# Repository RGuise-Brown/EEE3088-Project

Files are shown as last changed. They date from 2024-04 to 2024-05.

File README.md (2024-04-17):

# EEE3088-Project
This repository is used for the collaborative project to create a micromouse with the focus on creating a power and sensing unit which will work with an existing structure, motherboard and processor.This project is being completed by Rachael Guise-Brown and Heinrich Crous for EEE3088F at UCT.

Project Overview:

The project involves building subassemblies for a micro-mouse robot designed to navigate a maze within a set time limit. This repository focuses on the design and fabrication of the following modules:

Power Module: This module will be responsible for powering the motors, charging the battery, switching the robot on and off and providing an indication of the battery level to the processor.
Sensor Module: This module  will be responsible for detecting objects in the maze environment and relaying this information to the processor for navigation purposes.

Folder Structure:
power_module: This folder will contain all schematics, PCB design files, component selection information, and testing procedures related to the power module.
sensor_module: This folder will contain all design files, documentation, and testing procedures related to the sensor module.
documentation: This folder will contain any information documents linked to both power and sensor modules.

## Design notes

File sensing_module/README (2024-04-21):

This folder contains the following files:
1. My circuit schematic
2. Screenshots of the front and back of my PCB
3. A screenshot of my PCB in 3D viewer
4. My gerber files
5. My production files
6. My JLCPCB acceptance files
7. Datasheets for the TSAL4400, PD333, AND 2N3904

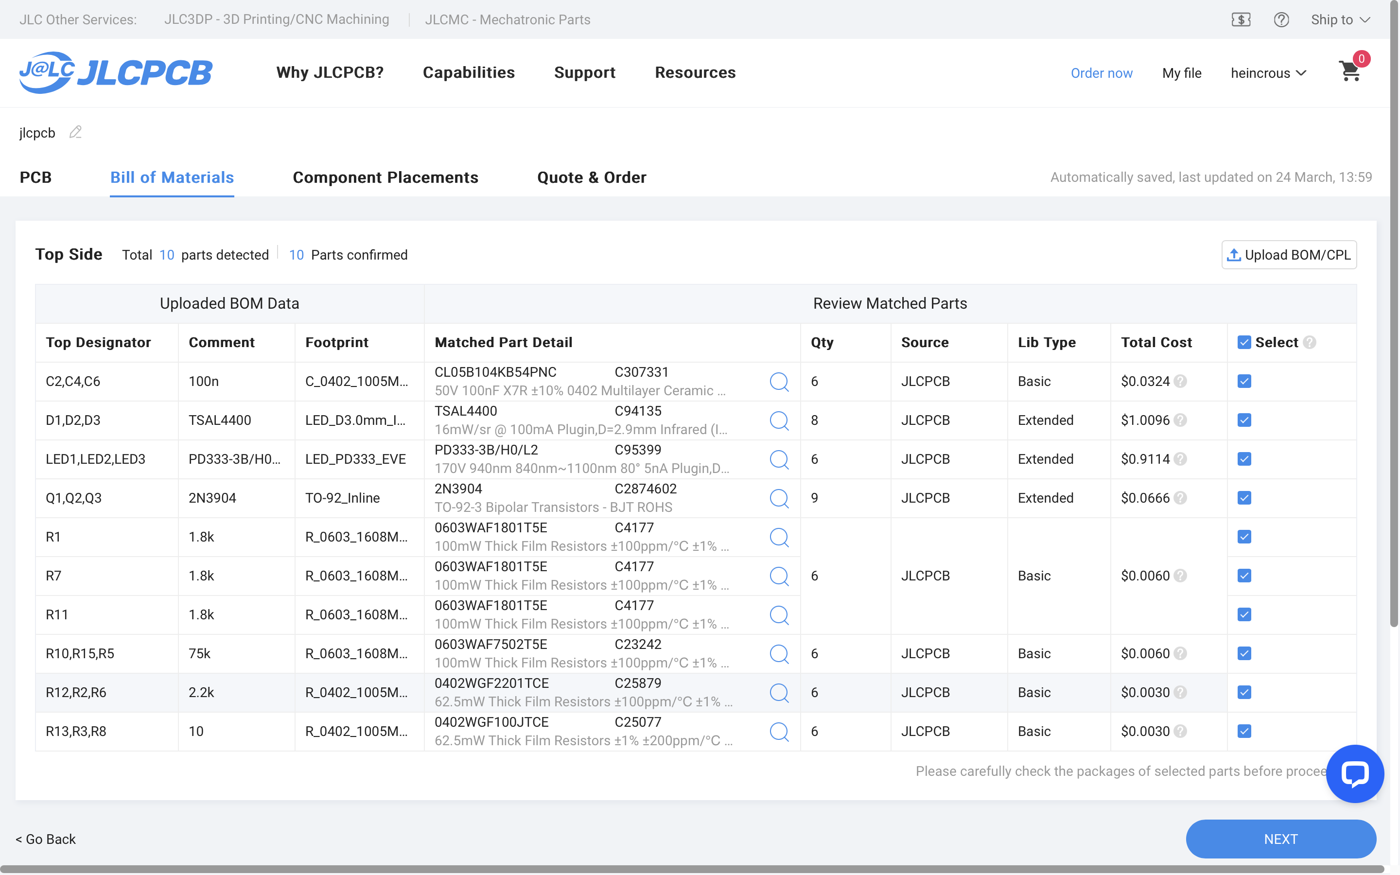
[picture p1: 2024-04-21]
sensing_module/production/EEE3088F_Project_JLCPCBBOM_CRSHEI004.png

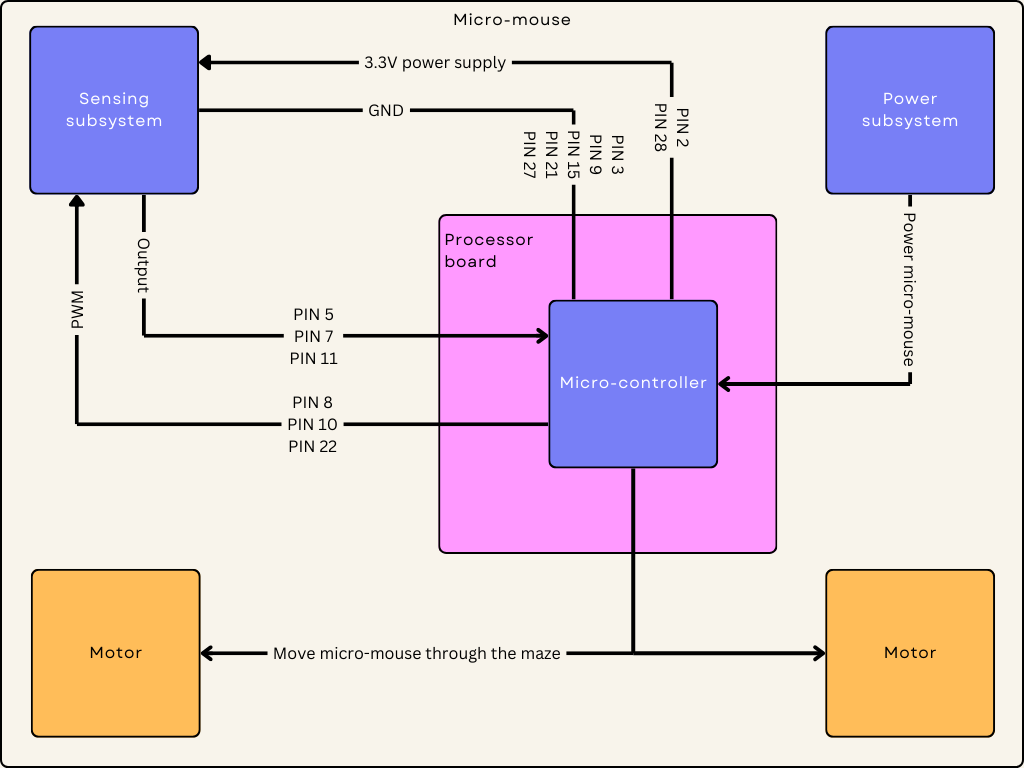
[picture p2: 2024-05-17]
sensing_module/Integration.png

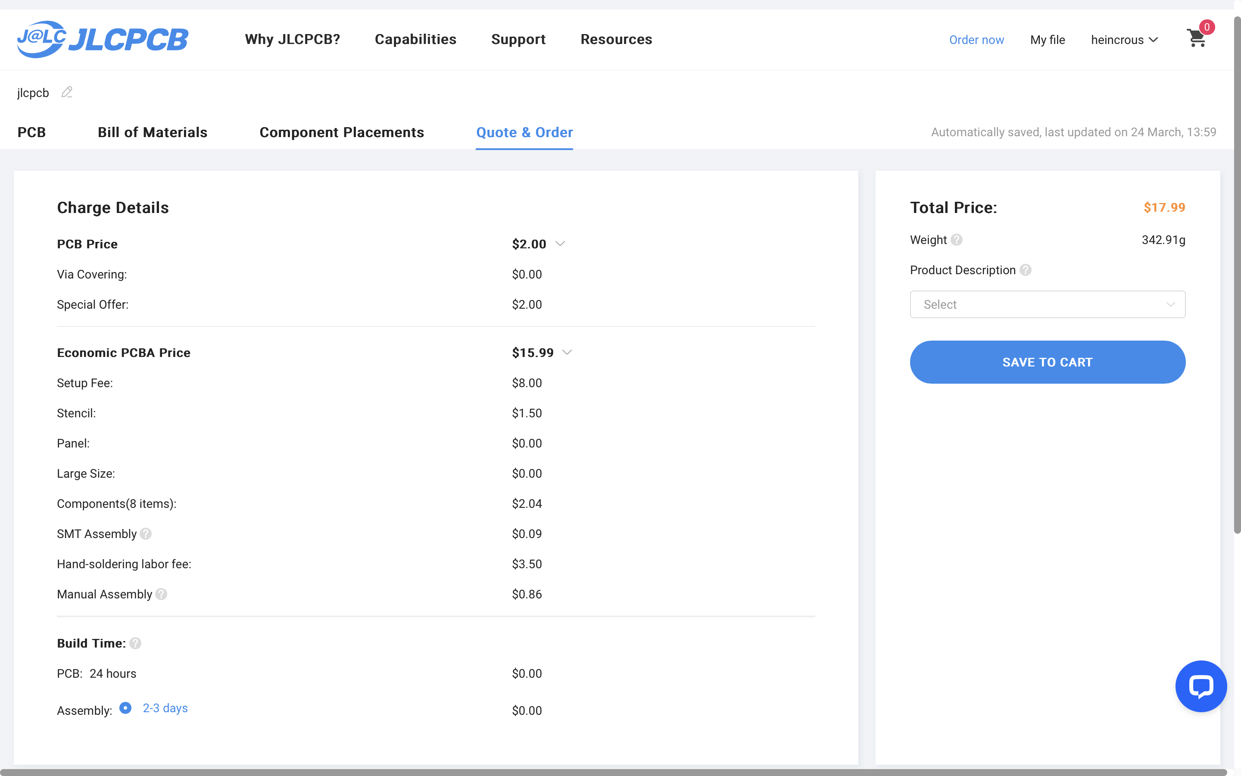
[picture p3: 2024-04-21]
sensing_module/acceptance/EEE3088F_Project_JLCPCBacceptance1_CRSHEI004.png

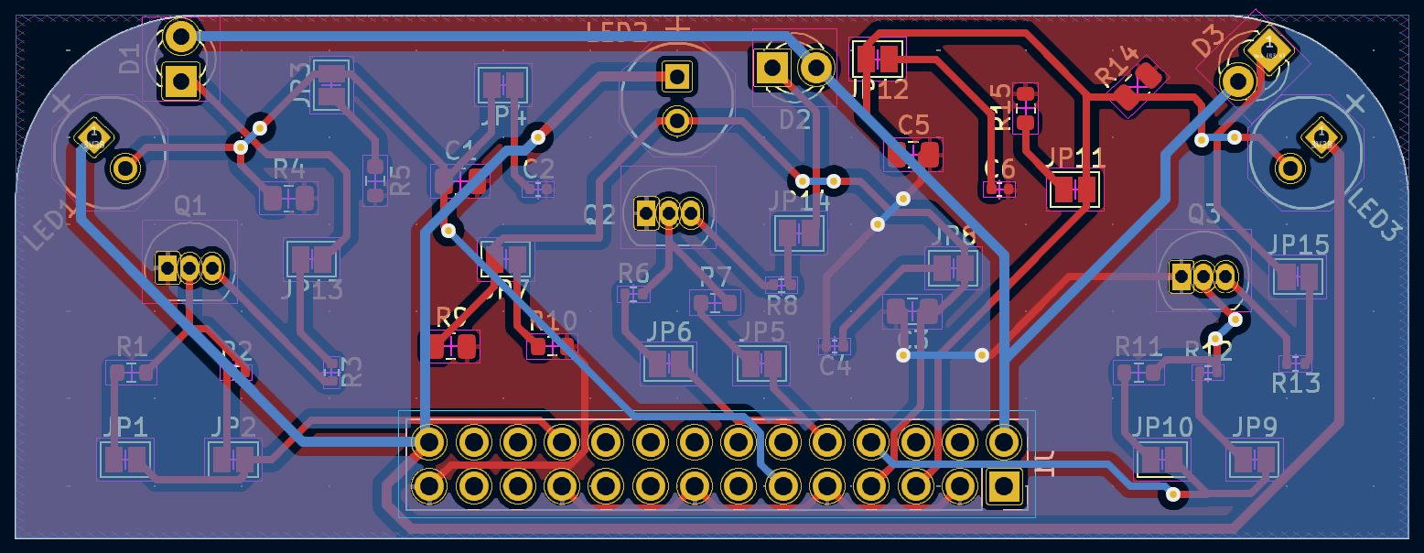
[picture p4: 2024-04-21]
sensing_module/Back.png

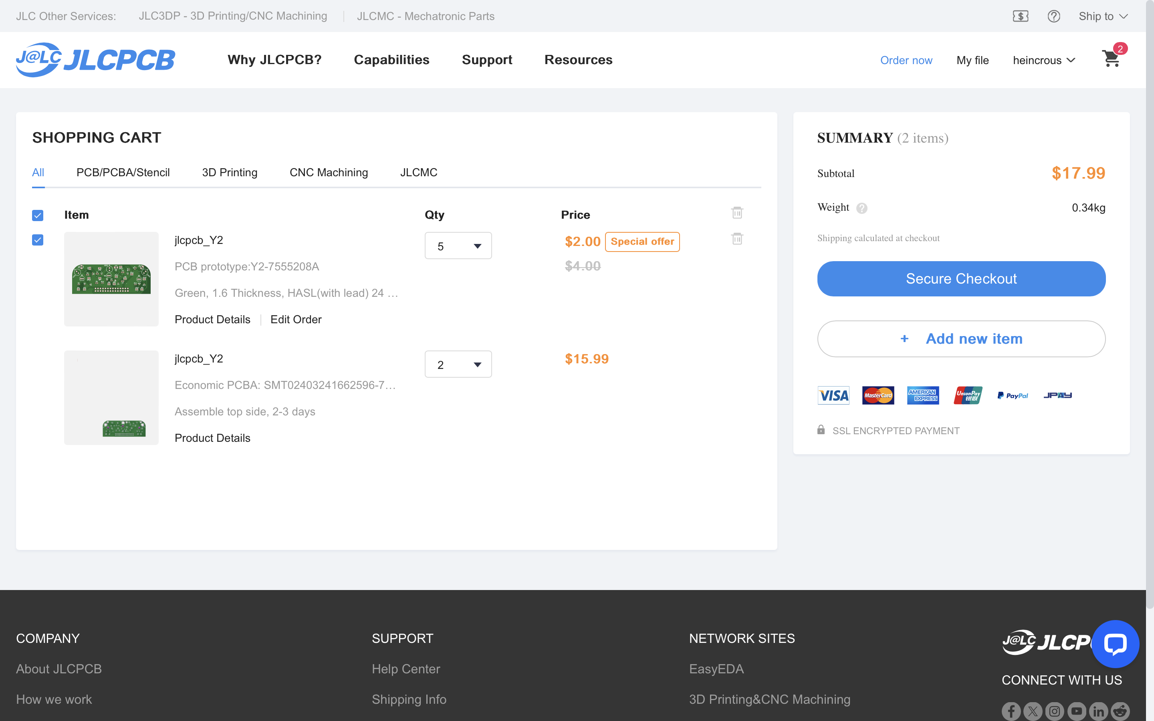
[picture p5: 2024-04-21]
sensing_module/acceptance/EEE3088F_Project_JLCPCBacceptance2_CRSHEI004.png

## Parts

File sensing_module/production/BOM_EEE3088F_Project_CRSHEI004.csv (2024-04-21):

Comment | Designator | Footprint | LCSC
75k | R10,R15,R5 | R_0603_1608Metric | C23242
10 | R13,R3,R8 | R_0402_1005Metric | C25077
2.2k | R12,R2,R6 | R_0402_1005Metric | C25879
2N3904 | Q1,Q2,Q3 | TO-92_Inline | C2874602
100n | C2,C4,C6 | C_0402_1005Metric | C307331
TSAL4400 | D1,D2,D3 | LED_D3.0mm_IRBlack | C94135
PD333-3B/H0/L2 | LED1,LED2,LED3 | LED_PD333_EVE | C95399
1.8k | R1 | R_0603_1608Metric
1.8k | R7 | R_0603_1608Metric
1.8k | R11 | R_0603_1608Metric

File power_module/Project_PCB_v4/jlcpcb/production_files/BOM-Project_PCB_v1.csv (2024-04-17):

Comment | Designator | Footprint | LCSC
1.2kR | R1 | R_0805_2012Metric | C17379
100R | R100,R_Fault1 | R_0805_2012Metric | C17408
10k | R10k1 | R_0805_2012Metric | C17414
1k | R1k1 | R_0805_2012Metric | C17513
3.0kR | R2,R3k1 | R_0805_2012Metric | C17661
470R | R_Stat1 | R_0805_2012Metric | C17710
510 | R510 | R_0805_2012Metric | C17734
2k | R_Prog1 | R_1206_3216Metric | C17944
4.7uF | C_Batt1,C_Vdd1 | C_0603_1608Metric | C19666
10uF | C_Vm1 | C_0603_1608Metric | C19702
LED_Red | D_Stat1 | LED_0603_1608Metric | C2286
LED_Green | Fault1 | LED_0805_2012Metric | C2297
2.2uF | C_Vint1 | C_0603_1608Metric | C23630
5.1k | R5.1 | R_0805_2012Metric | C27834
SS-12D10L5 | S1 | SW-TH_SS-12D10L5 | C319012
MCP73831-2-OT | Charge1 | SOT-23-5 | C424093
DRV8833PW | MD1 | TSSOP-16_4.4x5mm_P0.65mm | C50506
10nF | C_Vcp1 | C_0603_1608Metric | C57112

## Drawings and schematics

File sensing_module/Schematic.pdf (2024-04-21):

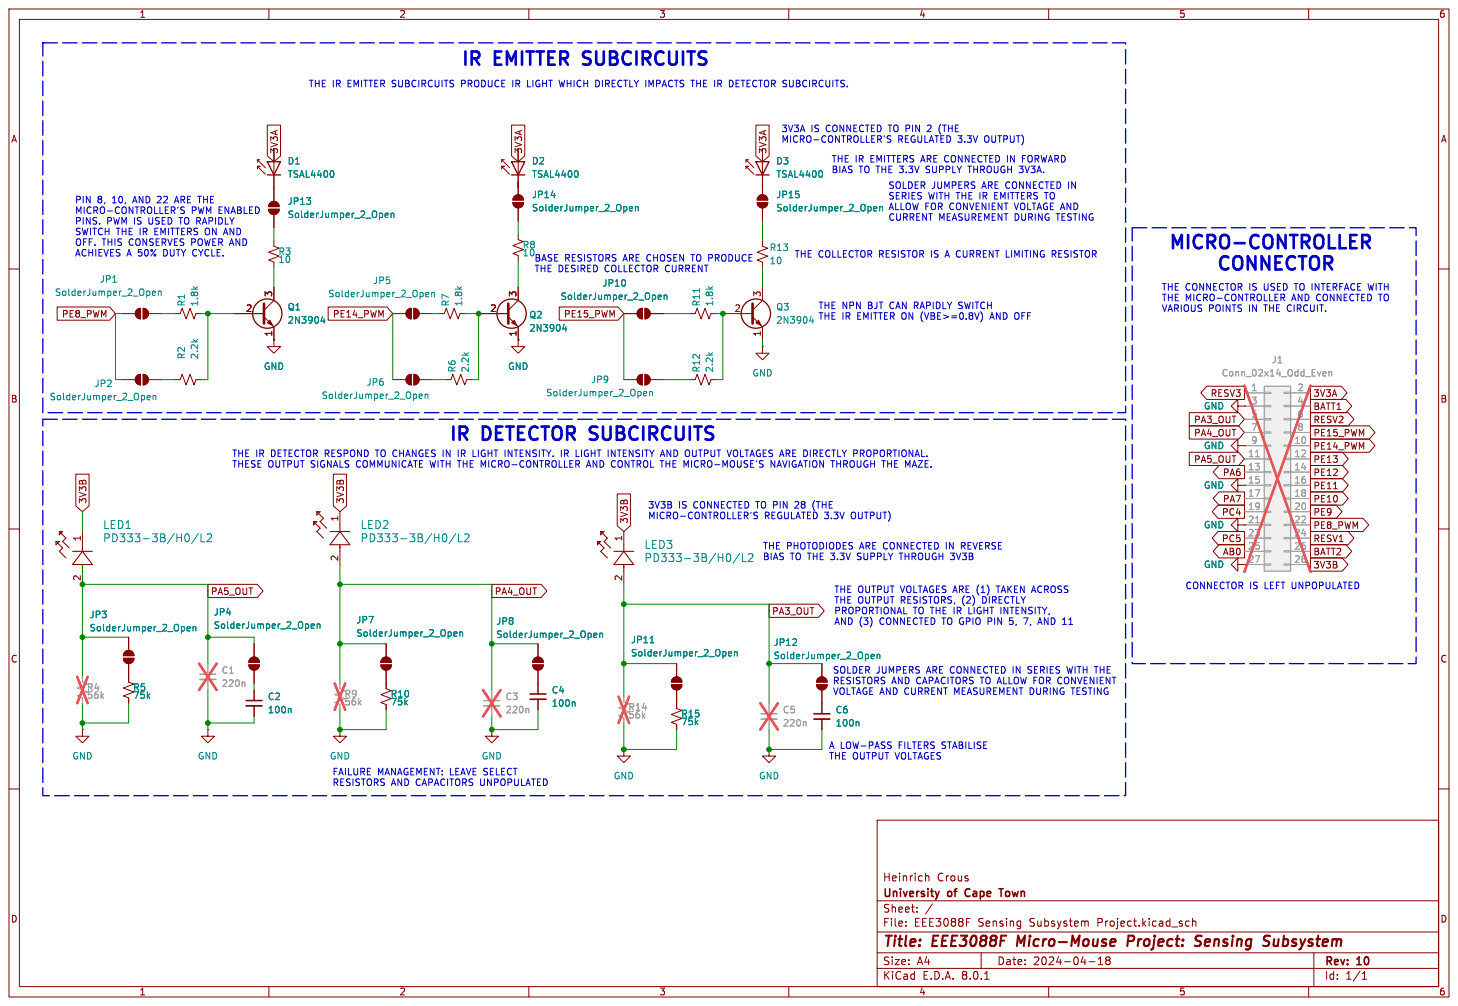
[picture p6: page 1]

VARIOUS POINTS IN THE CIRCUIT. THE IR EMITTER SUBCIRCUITS PRODUCE IR LIGHT WHICH DIRECTLY IMPACTS THE IR DETECTOR SUBCIRCUITS. BASE RESISTORS ARE CHOSEN TO PRODUCE
2N3904 D1 TSAL4400

THE IR DETECTOR RESPOND TO CHANGES IN IR LIGHT INTENSITY. IR LIGHT INTENSITY AND OUTPUT VOLTAGES ARE DIRECTLY PROPORTIONAL. THESE OUTPUT SIGNALS COMMUNICATE WITH THE MICRO-CONTROLLER AND CONTROL THE MICRO-MOUSE'S NAVIGATION THROUGH THE MAZE. 3V3A IS CONNECTED TO PIN 2 (THE MICRO-CONTROLLER'S REGULATED 3.3V OUTPUT)
D1 TSAL4400 Q1

THE IR EMITTERS ARE CONNECTED IN FORWARD
BIAS TO THE 3.3V SUPPLY THROUGH 3V3A. THE OUTPUT VOLTAGES ARE (1) TAKEN ACROSS

PIN 8, 10, AND 22 ARE THE MICRO-CONTROLLER'S PWM ENABLED

SERIES WITH THE IR EMITTERS TO
ALLOW FOR CONVENIENT VOLTAGE AND
CURRENT MEASUREMENT DURING TESTING

PINS. PWM IS USED TO RAPIDLY
SWITCH THE IR EMITTERS ON AND OFF. THIS CONSERVES POWER AND
10 GND
JP1 SolderJumper_2_Open

THE COLLECTOR RESISTOR IS A CURRENT LIMITING RESISTOR

THE CONNECTOR IS USED TO INTERFACE WITH
THE MICRO-CONTROLLER AND CONNECTED TO

THE NPN BJT CAN RAPIDLY SWITCH

J1 Conn_02x14_Odd_Even
9 GND GND GND GND GND

PROPORTIONAL TO THE IR LIGHT INTENSITY, AND (3) CONNECTED TO GPIO PIN 5, 7, AND 11 IR DETECTOR SUBCIRCUITS

BIAS TO THE 3.3V SUPPLY THROUGH 3V3B R5

THE OUTPUT RESISTORS, (2) DIRECTLY

SOLDER JUMPERS ARE CONNECTED IN SERIES WITH THE RESISTORS AND CAPACITORS TO ALLOW FOR CONVENIENT VOLTAGE AND CURRENT MEASUREMENT DURING TESTING

A LOW-PASS FILTERS STABILISE
THE OUTPUT VOLTAGES

FAILURE MANAGEMENT: LEAVE SELECT RESISTORS AND CAPACITORS UNPOPULATED

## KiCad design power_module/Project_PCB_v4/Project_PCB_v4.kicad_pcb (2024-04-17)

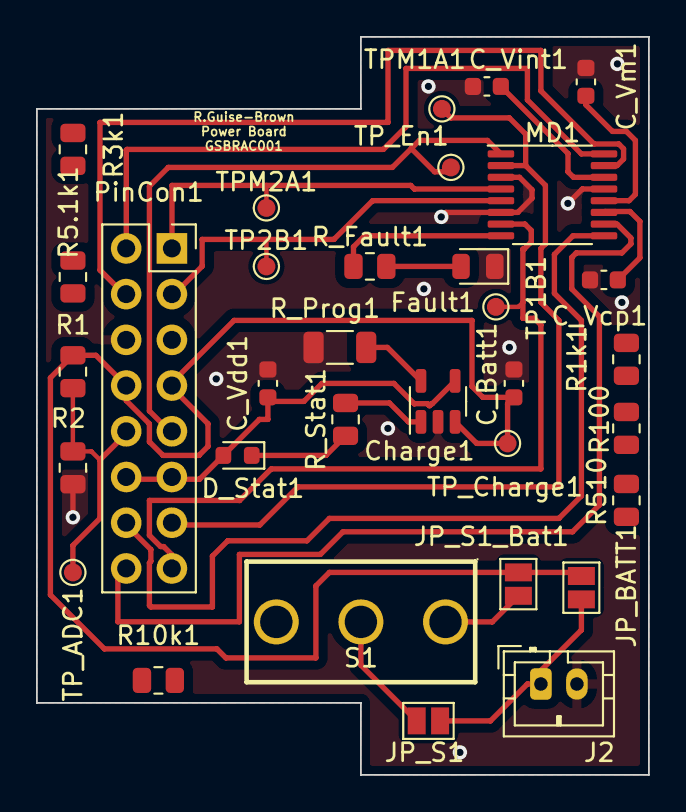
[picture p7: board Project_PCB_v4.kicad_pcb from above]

Board: 2 copper layers, 34.0 x 41.0 mm, 33 parts (0 on the bottom side), 24 nets.

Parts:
C_Batt1: 4.7uF; C_0603_1608Metric
C_Vcp1: 10nF; C_0603_1608Metric
C_Vdd1: 4.7uF; C_0603_1608Metric
C_Vint1: 2.2uF; C_0603_1608Metric
C_Vm1: 10uF; C_0603_1608Metric
Charge1: MCP73831-2-OT; SOT-23-5
D_Stat1: LED_Red; LED_0603_1608Metric
Fault1: LED_Green; LED_0805_2012Metric
J2: Conn_01x02; JST_PH_B2B-PH-K_1x02_P2.00mm_Vertical
JP_BATT1: Jumper_2_Open; SolderJumper-2_P1.3mm_Open_Pad1.0x1.5mm
JP_S1, JP_S1_Bat1: Jumper_2_Open; SolderJumper-2_P1.3mm_Open_Pad1.0x1.5mm
MD1: DRV8833PW; TSSOP-16_4.4x5mm_P0.65mm
PinCon1: Conn_02x08_Odd_Even; PinSocket_2x08_P2.54mm_Vertical
R1: 1.2kR; R_0805_2012Metric
R1k1: 1k; R_0805_2012Metric
R2: 3.0kR; R_0805_2012Metric
R3k1: 3k; R_0805_2012Metric
R5.1k1: 5.1k; R_0805_2012Metric
R10k1: 10k; R_0805_2012Metric
R100: 100R; R_0805_2012Metric
R510: 510; R_0805_2012Metric
R_Fault1: 100R; R_0805_2012Metric
R_Prog1: 2k; R_1206_3216Metric
R_Stat1: 470R; R_0805_2012Metric
S1: SS-12D10L5; SW-TH_SS-12D10L5
TP1B1, TP2B1: TestPoint; TestPoint_Pad_D1.0mm
TPM1A1, TPM2A1: TestPoint; TestPoint_Pad_D1.0mm
TP_ADC1: TestPoint; TestPoint_Pad_D1.0mm
TP_Charge1: TestPoint; TestPoint_Pad_D1.0mm
TP_En1: TestPoint; TestPoint_Pad_D1.0mm

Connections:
5V_1: C_Vdd1.1, Charge1.4 (VDD), D_Stat1.2 (A), PinCon1.11, PinCon1.12
BATT_1: C_Batt1.1, Charge1.3 (VBAT), JP_BATT1.2 (B), JP_S1_Bat1.1 (A), PinCon1.7, PinCon1.8, R1.1, TP_Charge1.1
BATT_ADC: PinCon1.10, R1.2, R2.2, TP_ADC1.1
GND: C_Batt1.2, C_Vcp1.1, C_Vdd1.2, C_Vint1.1, C_Vm1.2, Charge1.2 (VSS), Fault1.1 (K), J2.2, MD1.3 (AISEN), MD1.6 (BISEN), MD1.13 (GND), PinCon1.5, PinCon1.6, R2.1, R_Prog1.2
Motor1_A: MD1.2 (AOUT1), PinCon1.13, TPM1A1.1
Motor1_B: MD1.7 (BOUT1), PinCon1.15, TP1B1.1
Motor2_A: MD1.4 (AOUT2), PinCon1.1, TPM2A1.1
Motor2_B: MD1.5 (BOUT2), PinCon1.3, TP2B1.1
unnamed: C_Vcp1.2, MD1.11 (VCP)
unnamed: C_Vint1.2, MD1.14 (VINT)
unnamed: Charge1.1 (STAT), R_Stat1.2
unnamed: Charge1.5 (PROG), R_Prog1.1
unnamed: D_Stat1.1 (K), R_Stat1.1
unnamed: Fault1.2 (A), R_Fault1.2
unnamed: J2.1, JP_BATT1.1 (A), JP_S1.1 (A)
unnamed: JP_S1.2 (B), S1.2
unnamed: JP_S1_Bat1.2 (B), S1.1
unnamed: MD1.8 (nFAULT), R_Fault1.1
PC6-9 PWM1: MD1.16 (AIN1), PinCon1.2
PC6-9 PWM2: MD1.15 (AIN2), PinCon1.4
PC6-9 PWM3: MD1.9 (BIN1), PinCon1.14
PC6-9 PWM4: MD1.10 (BIN2), PinCon1.16
Reserve: MD1.1 (nSLEEP), PinCon1.9, TP_En1.1
VM: C_Vm1.1, MD1.12 (VM)

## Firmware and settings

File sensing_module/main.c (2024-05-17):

//====================================================================
// INCLUDE FILES
//====================================================================
#include "stm32f0xx.h"
#include <lcd_stm32f0.c>

//====================================================================
// LEFT THRESHOLDS
//====================================================================
const float threshold_voltage_left_upper = 2.7;
const float threshold_voltage_left_lower = 2.4;
    
//====================================================================
// MIDDLE THRESHOLDS
//====================================================================
const float threshold_voltage_middle_upper = 2.8;
const float threshold_voltage_middle_lower = 2.5;

//====================================================================
// RIGHT THRESHOLDS
//====================================================================
const float threshold_voltage_right_upper = 2.7;
const float threshold_voltage_right_lower = 2.4;

//====================================================================
// FUNCTION DECLARATIONS
//====================================================================
void helloWorld();
void init(void);
void loop();
void low_power_mode_enabled(void);
void low_power_mode_disabled(void);

//====================================================================
// MAIN FUNCTION
//====================================================================
int main (void)
{
    helloWorld();
    init();

    while (1) {
        loop();
        // low_power_mode_enabled();
        low_power_mode_disabled();

    }
}							

//====================================================================
// FUNCTION DEFINITIONS
//====================================================================
void helloWorld(){
    init_LCD();
    lcd_command(CLEAR);
    lcd_putstring("Slayyy");
}

void init(void){
    // Enable the clock to GPIO Port B
    RCC->AHBENR |= RCC_AHBENR_GPIOAEN; // Enable GPIOA clock
    RCC->AHBENR |= RCC_AHBENR_GPIOBEN; // Enable GPIOB clock

    GPIOA -> MODER |= GPIO_MODER_MODER3|GPIO_MODER_MODER7; // Set PA3-PA5 to analogue mode

    GPIOB -> MODER |= GPIO_MODER_MODER0_0|GPIO_MODER_MODER5_0|GPIO_MODER_MODER6_0|GPIO_MODER_MODER7_0; // Configure LED PB0, PB1, PB2, PB7 to outputs

    GPIOB -> ODR = 0x00; // Turn LEDs OFF

    // Configure PA11-PA13 as output
    GPIOA->MODER &= ~(3UL << (11 * 2)); // Clear bits for PA11
    GPIOA->MODER |= (1UL << (11 * 2));  // Set as general purpose output
    GPIOA->MODER &= ~(3UL << (12 * 2)); // Clear bits for PA12
    GPIOA->MODER |= (1UL << (12 * 2));  // Set as general purpose output
    GPIOA->MODER &= ~(3UL << (13 * 2)); // Clear bits for PA13
    GPIOA->MODER |= (1UL << (13 * 2));  // Set as general purpose output

    // Set initial output state
    GPIOA->ODR |= (1UL << 11); // Set PA11 high
    GPIOA->ODR |= (1UL << 12); // Set PA12 high
    GPIOA->ODR |= (1UL << 13); // Set PA13 high

    // Enable the clock to the ADC
    RCC -> APB2ENR |= RCC_APB2ENR_ADCEN;

    // Active ADC to be ready
    ADC1 -> CR |= ADC_CR_ADEN;
    while ( ((ADC1 -> ISR) & ADC_ISR_ADRDY) == 0 ); // wait for ADRDY flag to go high

    // Stop the ADC to configure parameters
    ADC1 -> CR &= ~ADC_CR_ADSTART;

    // ADC configuration
    ADC1 -> CFGR1 |= 0b00000000000000000000000000011000; // 12 bits
    ADC1 -> CFGR1 &= ~ADC_CFGR1_ALIGN; // right alignment
    ADC1 -> CFGR1 &= 0b00000000000000000010000000000000; // continuous mode
}

void loop(void) {
    uint16_t threshold_left_upper = threshold_voltage_left_upper / 3.3 * 4095; // Convert threshold voltage to ADC value (assuming 12-bit resolution)
    uint16_t threshold_middle_upper = threshold_voltage_middle_upper / 3.3 * 4095;
    uint16_t threshold_right_upper = threshold_voltage_right_upper / 3.3 * 4095;
    uint16_t threshold_left_lower = threshold_voltage_left_lower / 3.3 * 4095;
    uint16_t threshold_middle_lower = threshold_voltage_middle_lower / 3.3 * 4095;
    uint16_t threshold_right_lower = threshold_voltage_right_lower / 3.3 * 4095;
    
    //Select channel 3 and start ADC conversion
    ADC1->CHSELR = ADC_CHSELR_CHSEL3;
    ADC1->CR |= ADC_CR_ADSTART;
    
    // Wait for ADC conversion to complete
    while (!(ADC1->ISR & ADC_ISR_EOC));

    // Read ADC conversion result
    uint16_t adc_value_left = ADC1->DR;

    // Check if ADC value exceeds threshold for each channel
    if (adc_value_left > threshold_left_upper) {
        GPIOB->ODR |= (1UL << 7); // Turn on LED connected to PB7
        }

    else if (adc_value_left < threshold_left_lower){
        GPIOB->ODR &= ~(1UL << 7);
    }

    // Stop the ADC to configure parameters
    ADC1 -> CR &= ~ADC_CR_ADSTART;

    // Select channel 4 and start ADC conversion
    ADC1->CHSELR = ADC_CHSELR_CHSEL4;
    ADC1->CR |= ADC_CR_ADSTART;
    
    // Wait for ADC conversion to complete
    while (!(ADC1->ISR & ADC_ISR_EOC));

    // Read ADC conversion result
    uint16_t adc_value_middle = ADC1->DR;

    // Check if ADC value exceeds threshold for each channel
    if (adc_value_middle > threshold_middle_upper) {
        GPIOB->ODR |= (1UL << 6); // Turn on LED connected to PB6
        }
        
    else if (adc_value_middle < threshold_middle_lower){
        GPIOB->ODR &= ~(1UL << 6);
    }

    // Stop the ADC to configure parameters
    ADC1 -> CR &= ~ADC_CR_ADSTART;

    // Select channel 7 and start ADC conversion
    ADC1->CHSELR = ADC_CHSELR_CHSEL7;
    ADC1->CR |= ADC_CR_ADSTART;
    
    // Wait for ADC conversion to complete
    while (!(ADC1->ISR & ADC_ISR_EOC));

    // Read ADC conversion result
    uint16_t adc_value_right = ADC1->DR;

    // Check if ADC value exceeds threshold for each channel
    if (adc_value_right > threshold_right_upper) {
        GPIOB->ODR |= (1UL << 5); // Turn on LED connected to PB5
        }
        
    else if (adc_value_right < threshold_right_lower){
        GPIOB->ODR &= ~(1UL << 5);
    }

    // Stop the ADC
    ADC1 -> CR &= ~ADC_CR_ADSTART;
}

void low_power_mode_enabled(void){
    // 80% duty cycle - 20% reduction in power consumption
    GPIOB->ODR |= GPIO_ODR_0;
    GPIOA->ODR |= (1UL << 11); // Set PA11 high
    GPIOA->ODR |= (1UL << 12); // Set PA12 high
    GPIOA->ODR |= (1UL << 13); // Set PA13 high

    // adjust delay to change duty cycle
    delay(200);

    GPIOB->ODR &= ~GPIO_ODR_0;
    GPIOA->ODR &= ~(1UL << 11); // Set PA11 low
    GPIOA->ODR &= ~(1UL << 12); // Set PA12 low
    GPIOA->ODR &= ~(1UL << 13); // Set PA13 low

    delay(50); // f = 4kHz
    }

void low_power_mode_disabled(void){
    GPIOA->ODR |= (1UL << 11); // Set PA11 high
    GPIOA->ODR |= (1UL << 12); // Set PA12 high
    GPIOA->ODR |= (1UL << 13); // Set PA13 high
    }

//********************************************************************
// END OF PROGRAM
//********************************************************************
